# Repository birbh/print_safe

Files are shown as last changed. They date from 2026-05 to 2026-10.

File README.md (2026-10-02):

# print_safe
Print safe is a smart biometric storage system designed for students and teachers to securely store their personal belongings.
This project combines fingerprint based access controls,breach detection and activity logging which helps in preventing the unauthorized access.

Screenshot 2026-10-03 at 1 48 07 AM

## What is this project??
Print safe is an intelligent locker system that allows only authorized person to access stored items using their fingerprint.

Unlike basic locks; it doesnt just opens or closes it but::
- Verifies the identity using fingerprint sensor
- Detects forced access or tampering
- Logs all the access attempts(all including successful and failed one) 

This thing makes it suitable for places like schools,hostels and even a shared living spaces.

## How do you use it? 

1. For Daily Use:
    - Place your registered finger on the sensor:

    1. If fingerprint matches:
        - Servo rotates to unlock the storage
        - Green LED will turn on indicating success
        - A success beep will sound from the buzzer
        - Oled display will show "Access Granted" along with clock
        - The safe will automatically lock after 5 secs(initially)
    2. If fingerprint does not match:
        - Red LED will turn on indicating failure
        - A failure beep will sound from the buzzer
        - Oled display will show "Access Denied" 
    - To lock manually:
        - Press the green push button switch to lock the safe immediately
        - Oled display will show "Door Locked"

2. For Admin Use:
    - To enter admin mode:
        - Press and hold both the green and red push button switch for 5 seconds 
        - The safe will play double beep and oled will show "Admin Mode" and then "Place finger to register"
        1. To register a new fingerprint:
            - Place the new finger on the sensor
            - The system will capture first scan and prompt 'Remove finger'
            - Lift the finger from the sensor
        2. When screen prompts 'Place same finger again':
            - Place the same finger again on the sensor to confirm
        - If successfull, buzzer will play a success tone and oled will show "Fingerprint Registered"

3. Security and resets:
    - Tamper alarm:
        - If an unregistered finger is scanned 3 times in a row, the system will trigger a tamper alarm:
            - Buzzer will sound continuously with loud beeps
            - Red LED will flash rapidly
            - The biometric system will be locked to prevent further attempts
    - To reset the system:
        - Press the red push button which is hidden in the side of the safe
        - This will reset the siren
        - Clear the failed attempt count
        - Allow users to try accessing again
        - Again ready to scan fingerprints

## Story behind this:

### Why am i making this? 
I lived in my school's hostel in my school life. The main problem of hostel life was that my belongings never stayed in my place. Someone always came to my place and misplace my personal belongings, which would frustate me and I used to be very angry as:
- my items were not always where i left them
- there was no way to know who accessed them
- privacy was very hard to maintain

To solve this problem for hostel students, I thought of creating a system to:
- protect belongings
- ensure authorized access
- let user know if system was tampered or not

### How the idea came in my mind?
The idea actually came from my own room at home. One day while i was sitting in my bed, I thought that I don't have privacy maintained in my room. While i was sleeping i thought of keeping a fingerprint scanning device in my room's entrance that would only unlock the room if the fingerprint would match to me. I thought,'Why not make my own custom device at home buying all the parts from the market🤔'. But I never made it 😭.

**print_safe** is my attempt to bring these ideas to life, solving real world problem I personally faced.

## Project preparation instructions:

Printsafe is designed to be fully robust, utilizing mechanical fastners and 3d-printed components.

### Component fastening instructions:
1. Dev boards(Arduino,rtc,boost conv.,charging module,etc): 

    They are mounted to the floor of enclosure using screws through its screw mounting holes.
2. Locking Servos:

    They are slid into custon 3D-printed mounting cages(as in the 3D model) and secure tightly with screws to prevent torsion during locking sequences.
3. Enclosure Door:

    Attached to the main body via dual screw mechanical hinge layout.
4. Door alignment and security:

    A high strength magnetic latch is alighed on the interior frame to provide tactile door retention, ensuring the door remains fixed to the frame so the servo deadbolts can smoothly engage and lock the system.

### Step by step assembly:
1. Prepare the shell:

    3D print the main enclosure body and door panel using the provided 'CAD' files in the repo(recommended: PLA/PETG).
2. Mount the core electronics:

    Secure the Arduino and other similar electronic componects directly into the 3Dprinted mounts given in CAD files as in Onshape.
    Similarly using the dedicated heaavy duty double sided tape of breadboards mount it into the wall as in CAD.Many breadboards already come with a peel-and-stick adhesive backing. Clean both the back of the breadboard and the wall thoroughly before applying.
3. Install servo mounts:

    Screw the 3D printed servo brackets into the interior left wall as in CAD. Slide the servos into the brackets and secure them easily.
4. Hinge and latch attachment:

    Screw the physical hinge to both the interior side wall and the door panel.Mount the magnetic latch components to ensure the tight, aligned seal when the door swings shut.
5. Calibrate the lock position:

    Power the electronics so the servos rotate to their default locked positions, then attach the locking arms to perfectly block door path when closed.
(NOTE: the 3d models are available in fully assembled and parts form in the repo itself. they are refecenced mostly from grabcad and other 3d model libraries.)

### What was challenging and things to be noted??(overall)
There were many challenges making this project. Here i am listing some important things to be noted to make this project on the basis of what i faced in irl build.
- First, it was challenging to make this project fully eco-friendly by using only cardboards and papers. Every small to big things for the project were made from cardboard but for anyone making this I would recommend using a 3d printed case and components which would help a lot in saving time and efficiency.(I couldnt use 3d printed parts cause it takes 3-4 months and huge tax to deliver from abroad and there are not trusted 3d printing platform in my country.
- The logic behind the door opening and closing seems easy in CAD but its a bit complicated as, in my case, servo didnt directly attach to the door so I was forced to use a cardboard extension which attaches to servo head and the door too. But doing this made the cardboard extension move left and right along the door when the servo started to work. So to tackle this I applied the hot glue to the other end of extension and attached it to door and instantly turned and run the device 4 to 5 times which made the glue flexible and the problem was somehow solved but i found that the door dosnt fully close due to the flexible glue. so for this prototype version this issue was not solves and i managed to close it with my hand for the remaining part which then would attach to the magnets inside and holds the door in fixed position. Hence, the 3d printed fixed parts could have solved it.
- Also keep in mind that you dont join the boost converter in opposite direction as it would burn the internal components and you'll have to buy a new one as i did.
- Make sure the batteries are connected in parallel as i. did which would provide a good balanced voltage to the boost converter. 
- This time when i tried to attach the oled, fingerprint sensor and leds to the cardboard door, they were so heavy for the cardboard to handle so i had to change the whole design if my door only letting the oled display attach to the door while moving.
- Last challenge was to provide the essential torque to the door through servos to overcome the magnetic forse between the magnets attached to the end of the door and inner wall of door. So to match the torque of servos I taped the magnet's outer parts and then attached to the door which eventually reduced the magnetic force between the magnets and it was easier for servos to overcome the force. So i recommend using more powerful servos than the standard blue SG90 servos.

That's it!!! If you keep these challenges in mind and work for project, you'd definitely make this project easily in most efficient way.

## why this and why is it unique?
- its not just a lock but decision based security system
- combines verification + intrusion + logging
- designed for real world student problems

## where can it be used ??
- hostel lockers
- school storage system
- personal drawers and cabinets
- shared living spaces

## IRL Build:
### Pictures:
tempImageHhVQ3i
tempImage1bL4IE
tempImageRyGA7T
tempImageo10fXb
tempImage0Veda7
tempImageZshb4o
tempImagegbeKXF
tempImagegSR62w

### Demo Video:
Youtube: [Demo Video](https://www.youtube.com/watch?v=nzNCS3ORe8U)

## CAD:
Screenshot 2026-08-04 at 6 19 32 PM
Screenshot 2026-08-04 at 6 20 45 PM
Screenshot 2026-08-04 at 6 21 53 PM
Screenshot 2026-08-04 at 6 22 24 PM
Screenshot 2026-08-04 at 6 29 24 PM
Screenshot 2026-08-04 at 6 30 27 PM

For those who want to see full design, here's the like to the Onshape CAD model:

[Onshape Model](https://cad.onshape.com/documents/6a9e66424898c3a5d22b5a59/w/668f054415e8574befa880c0/e/08491907242ab19b0f76189a)

## Circuit Diagram:
I made the circuit diagram for my project using tikercad. Due to absence of required components i have used Breadboard to complete the circuit diagram and used the notes feature in tinkercad😅.

   ### SS:
   Main circuit
battery,charging,boost circuit

   ### Links to tinkercad:
   
   [Main circuit](https://www.tinkercad.com/things/bx13RGkoUNs-printsafe-cc/editel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)
   
   [Battery and charging circuit](https://www.tinkercad.com/things/15RenR3HXBn-charging-and-boost/editel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)

## Components required(planned):

- Arduino uno with cable
- AS608 Fingerprint Module
- Servo motor
- Leds
- Active Electronic Buzzer
- Resistors (10k Ω)
- Resistors (220 Ω)
- WIRES
- Breadboard
- Push Button Switches
- 18650 Battery Holder
- 18650 Lithium-Ion Battery
- TP4056 Charging Module
- MT3608 Boost Converter(or equivalent)
- I2C OLED Display 0.96 inch
- DS3231 RTC Module
- ESP8266 NodeMCU(optional)
- 1000μF (Polarized)(greater than 5V)
- Switch (on/off)
- Battery to DC barrel jack(for arduino)
- 3D models as stated above.

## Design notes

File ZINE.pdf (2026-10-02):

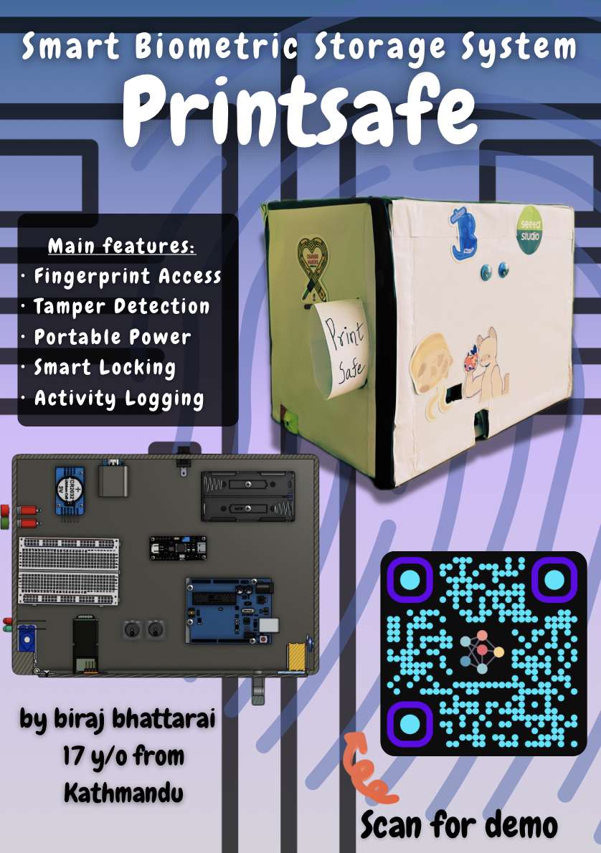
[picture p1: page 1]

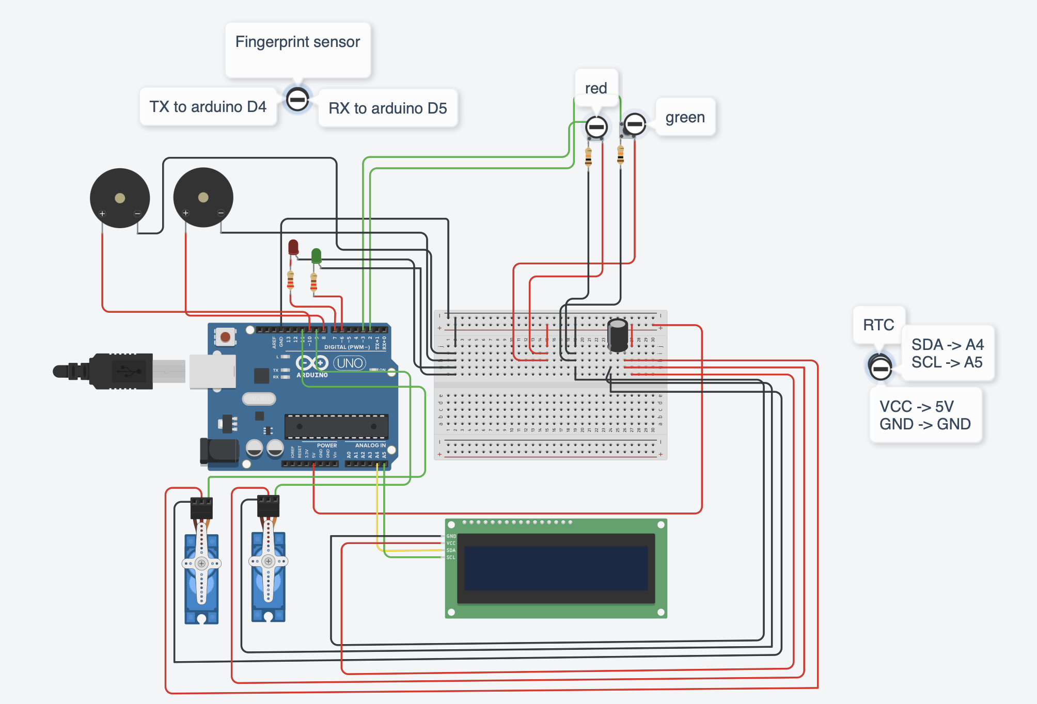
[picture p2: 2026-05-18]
Circuits/Main circuit.png

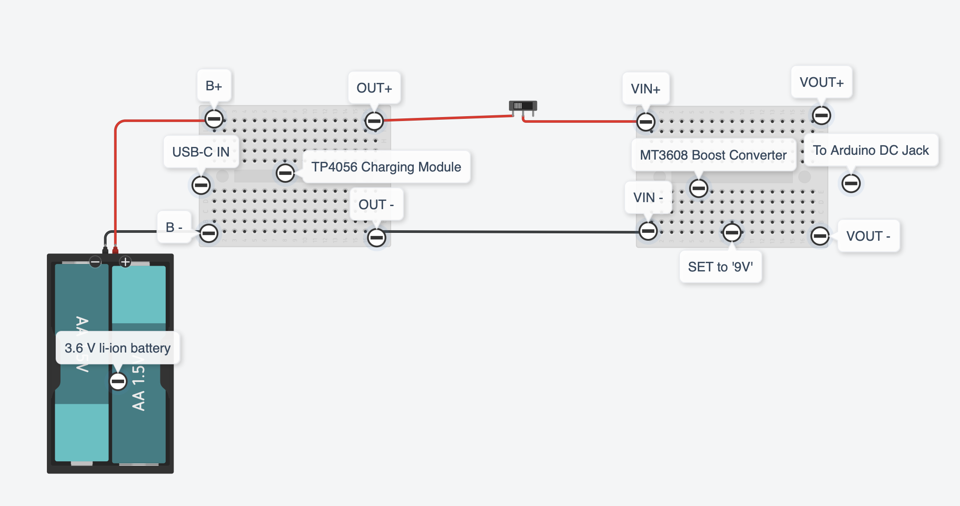
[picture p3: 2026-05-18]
Circuits/battery,charging,boost circuit.png

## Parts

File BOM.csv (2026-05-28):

Items | Price | Link | Quantity
Arduino uno with cable | ~20$ | https://shorturl.at/WWEXE | 1
AS608 Fingerprint Module | $15-20$ | https://shorturl.at/U69mB | 1
Servo motor | $8 | https://shorturl.at/Ip8lg | 2
Leds | $7 | https://shorturl.at/RFGpo | Pack
Active Electronic Buzzer | ~$7 | https://shorturl.at/qj3BP | Pack
Resistors (10k Ω) | $6 | https://acesse.one/ls03mpb | Pack
Resistors (220 Ω) | $5 | https://l1nk.dev/5dzzufx | Pack
Wires(jumper) | $8 | https://l1nk.dev/i9meakx | Pack
Wires(Normal) | ~4$ | https://shorturl.at/ygMDc | Pack
Aluminium foil(optional) | $9 | https://acesse.one/0dw1c65 | 1
Breadboard | $10 | https://l1nk.dev/uzbsl38 | 1
Push Button Switch | $3 | https://l1nk.dev/vnitg2r | 2
18650 Battery Holder | $3 | https://l1nk.dev/oosg72w | 1
18650 Lithium-Ion Battery | $3 | https://l1nq.com/20qpqqt | 1
TP4056 Charging Module | $6 | https://l1nk.dev/wedzzh9 | 1
MT3608 Boost Converter | $6 | https://l1nk.dev/9jh41ry | 1
I2C OLED Display 0.96 inch | $8 | https://l1nk.dev/515rwpb | 1
DS3231 RTC Module | $5 | https://l1nk.dev/nx8q5ky | 1
ESP8266 NodeMCU(optional) | $7 | https://l1nk.dev/9cr6knm | 1
M3 Screw Set(optional) | $6 | https://l1nk.dev/izsoxws | Pack
Acrylic Sheet(Optional) | $9 | https://acesse.one/pnp6sq5 | 1
Mini Hinges | $4 | https://l1nk.dev/g1qcra8 | 2
Magnetic Latch | $7 | https://l1nk.dev/61dy1q1 | 1
1000μF (Polarized)(greater than 5V) | $3-$7 | https://www.ebay.com/itm/255390041576 | 1
Switch (on/off) | ~2$ | https://tinyurl.com/ycyaypbw | 1
Battery to DC barrel jack(for arduino) | ~1$ | https://shorturl.at/GKWPJ | 1
3D printing filament | ~$8-$14 | https://l1nk.dev/jvyhtj1 | 1
Total: | ~170$

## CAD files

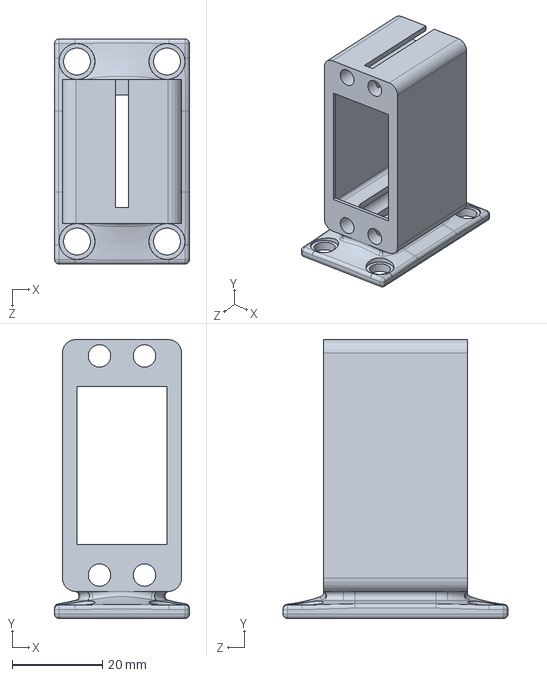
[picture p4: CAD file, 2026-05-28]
CAD/Parts files/Servo Mount (Standing).SLDPRT
30.0 x 62.0 x 50.0 mm

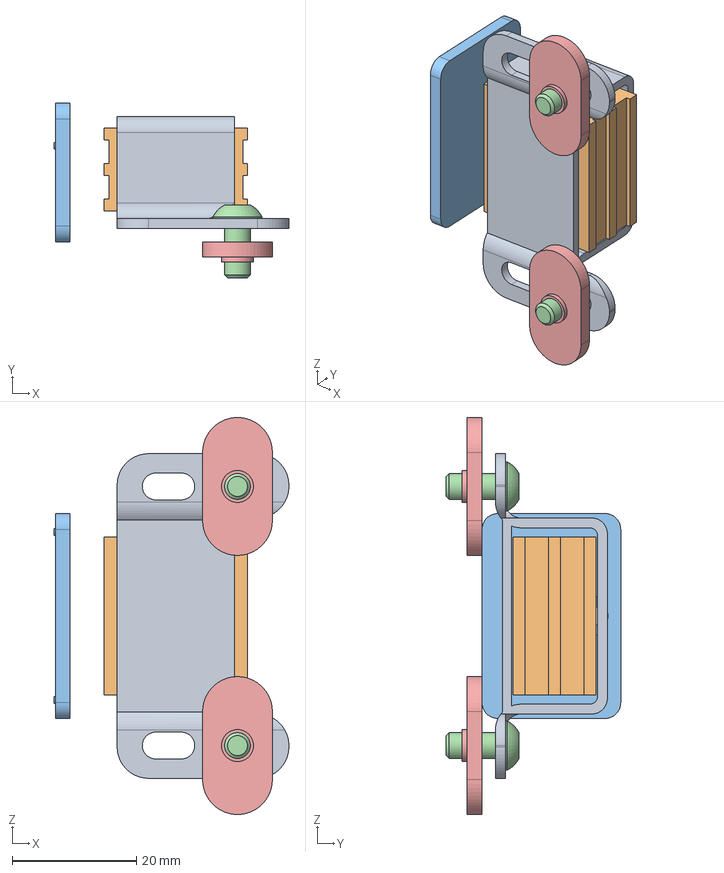
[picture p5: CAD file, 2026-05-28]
CAD/Parts files/2090.stp
37.8 x 28.1 x 64.0 mm
2090_a
2090_magnet
2090_b

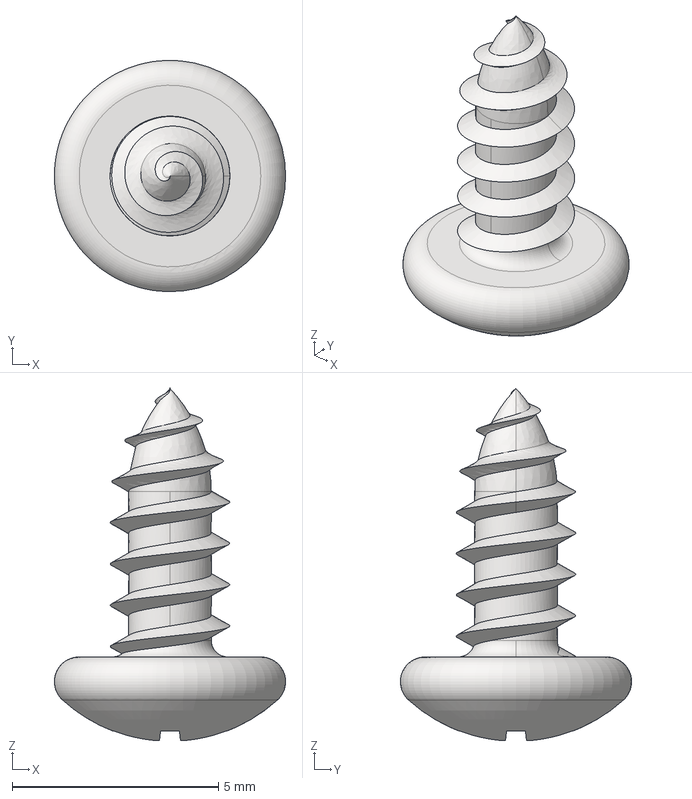
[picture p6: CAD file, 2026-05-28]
CAD/Parts files/lmed scc.stp
5.60 x 5.60 x 8.52 mm

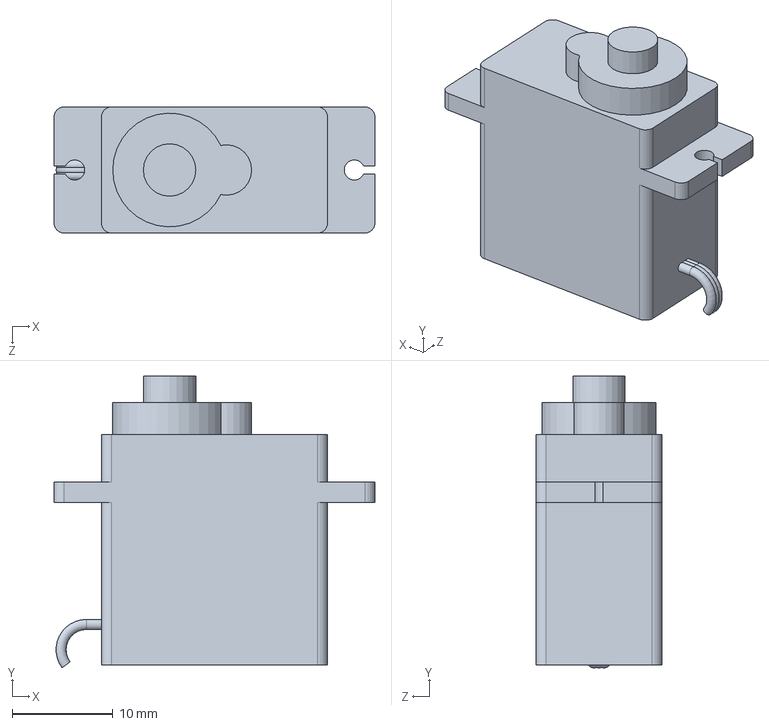
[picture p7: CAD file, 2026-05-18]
CAD/Parts files/Servo_SG90.SLDPRT
31.8 x 28.9 x 12.5 mm

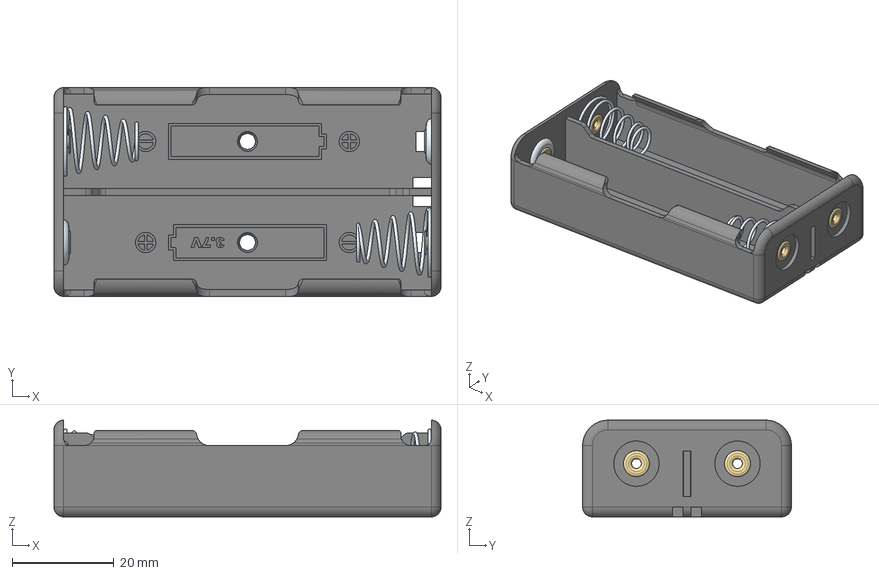
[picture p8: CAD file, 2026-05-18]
CAD/Parts files/BATTERY HOLDER x2.stp
76.0 x 41.0 x 19.0 mm
Porta baterias 2x18650
Contacto_Helice_v2.0 x 2
Contacto_plano_v1.0 x 2
remache_v1.0 x 4

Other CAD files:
CAD/Assemblies/Main assembly.step
CAD/Assemblies/box.step
CAD/Parts files/MoboSpeakerHolder.step
CAD/Parts files/Part Studio 1.step
CAD/Parts files/ActiveBuzzer_TMB12A05.step
CAD/Parts files/Fingerprint Reader.step
CAD/Parts files/Green Push Button.step
CAD/Parts files/TP4056_Charging_Module_Type_C.step
CAD/Parts files/LED D5 - Red.step
CAD/Parts files/Red Push Button.step
CAD/Parts files/Part Studio 2.step
CAD/Parts files/LED D5 - Green.step
CAD/Parts files/DS3231 RTC.step
CAD/Parts files/M4 Hex Screw v2.step
CAD/Parts files/Mensan KP-01 Plastik Kulp.SLDPRT
CAD/Parts files/OLED TEMU 0.96 in.stp
CAD/Parts files/Wood_Screw_Flat_Head_Phillips.SLDPRT
CAD/Parts files/bolt.SLDPRT
CAD/Parts files/m3-5mm.sldprt

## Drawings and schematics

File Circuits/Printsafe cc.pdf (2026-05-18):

A

1 | 2 | 3 | 4 | 5 | 6

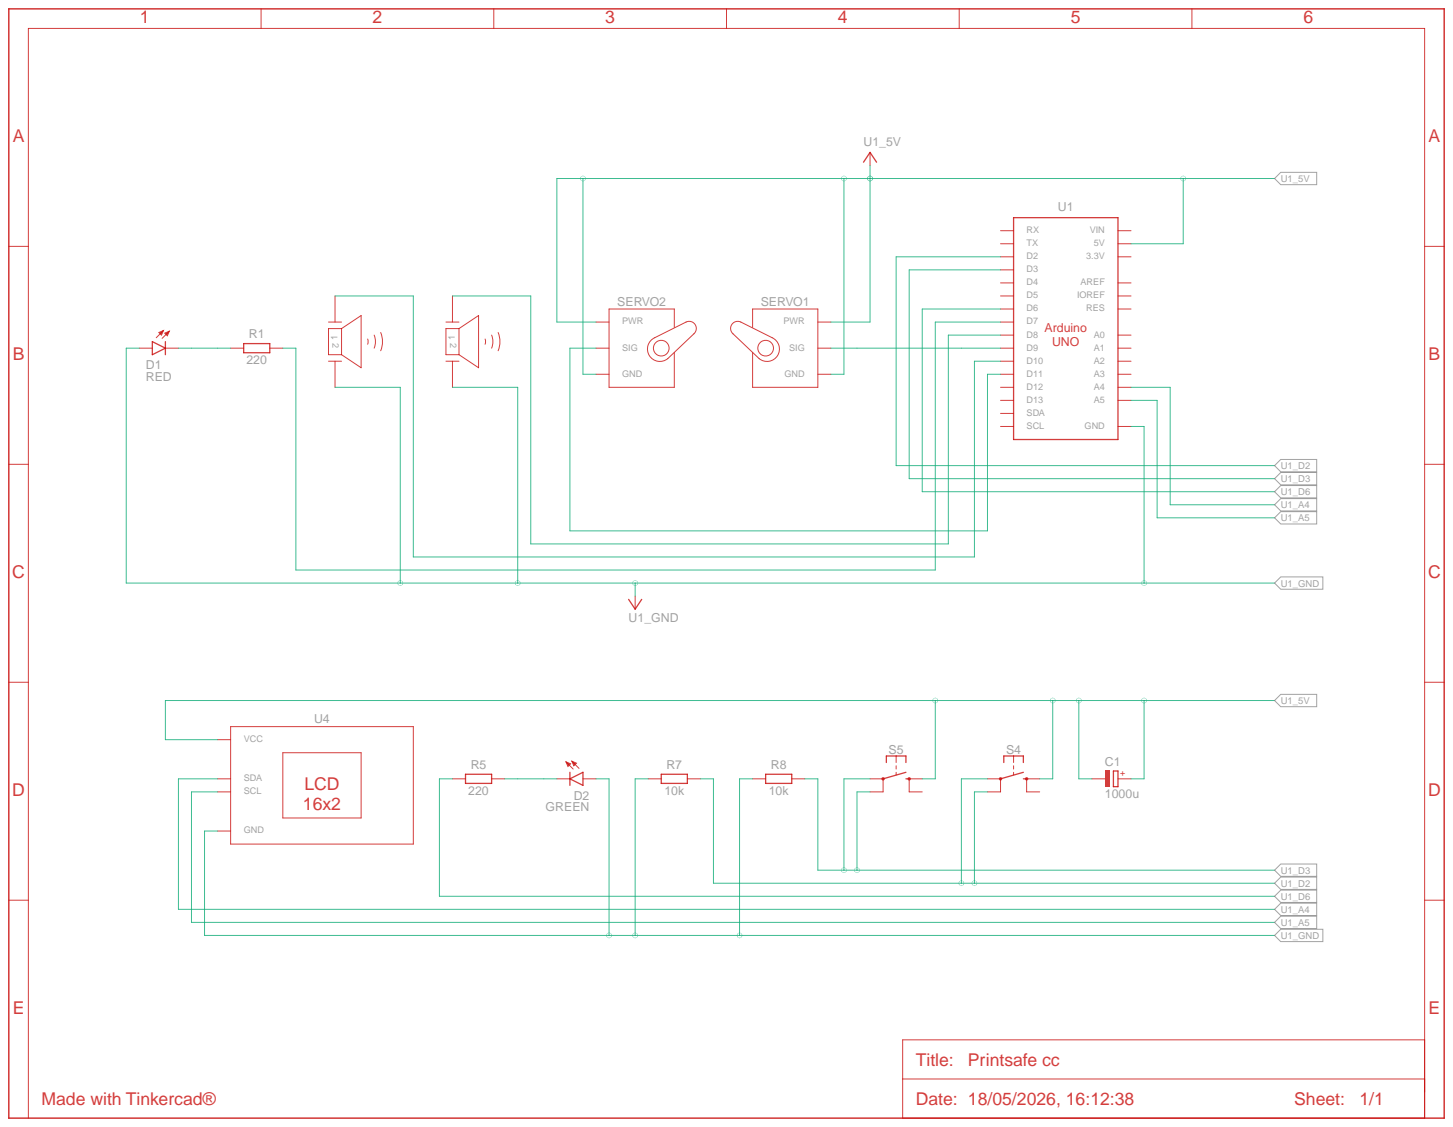
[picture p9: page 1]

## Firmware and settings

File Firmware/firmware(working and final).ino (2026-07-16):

#include <Servo.h>
#include <Adafruit_Fingerprint.h>
#include <Wire.h>
#include <RTClib.h>
#include <Adafruit_GFX.h>
#include <Adafruit_SSD1306.h>

// --- OLED Screen Configuration ---
#define SCREEN_WIDTH 128
#define SCREEN_HEIGHT 64
#define OLED_RESET    -1 
Adafruit_SSD1306 display(SCREEN_WIDTH, SCREEN_HEIGHT, &Wire, OLED_RESET);

// --- Verified Pin Allocations ---
const int greenBtnPin = 4;    // Green Button: Manual Lock / Admin Combo
const int redBtnPin = 5;      // Red Button: Hidden Alarm Reset / Admin Combo
const int greenLedPin = 6;
const int redLedPin = 7;
const int buzzerAPin = 8;     
const int servoupPin = 9;     
const int buzzerBPin = 10;    
const int servodownPin = 11;   

// --- Object Initializations ---
Servo servoup;
Servo servodown;
RTC_DS3231 rtc;

// Fingerprint Sensor Serial Configuration
SoftwareSerial mySerial(2, 3);
Adafruit_Fingerprint finger = Adafruit_Fingerprint(&mySerial);

// --- Global System State Variables ---
int failedAttempts = 0;
const int maxFailedAttempts = 3;
const int stepDelay = 15; 

bool isLocked = true;          // Tracks the physical lock status of the vault
bool systemBlock = false;       // Hardlock flag when tamper alarm is tripped
unsigned long unlockTime = 0;  // Tracks auto-relock window countdowns
const unsigned long autoLockDelay = 30000; // 30 seconds lock window

void setup() {
  Serial.begin(9600);
  delay(500); 
  Serial.println(F("\n============================================="));
  Serial.println(F("         PRINTSAFE PRO STANDALONE FIRMWARE    "));
  Serial.println(F("============================================="));

  // Configure Button Pins with Internal Pull-Ups
  pinMode(greenBtnPin, INPUT_PULLUP);
  pinMode(redBtnPin, INPUT_PULLUP);
  
  pinMode(greenLedPin, OUTPUT);
  pinMode(redLedPin, OUTPUT);
  pinMode(buzzerAPin, OUTPUT);
  pinMode(buzzerBPin, OUTPUT);

  // Initialize OLED
  if(!display.begin(SSD1306_SWITCHCAPVCC, 0x3C)) { 
    errorBlink(3); 
  }
  
  display.clearDisplay();
  display.setTextSize(1);
  display.setTextColor(SSD1306_WHITE);
  display.setCursor(20, 25);
  display.setTextSize(2);
  display.println(F("PRINTSAFE"));
  display.display();
  delay(1500);

  // Initial Servo Alignment (Locked State at 0 Degrees)
  servoup.attach(servoupPin);
  servodown.attach(servodownPin);
  servoup.write(0);
  servodown.write(0); 
  delay(200);
  servoup.detach(); // Cut power to prevent inrush brownouts during setup
  servodown.detach();
  isLocked = true;

  // Initialize Clock
  if (!rtc.begin()) {
    updateOLEDStatus(F("RTC ERROR"), F("Check Wiring"));
    errorBlink(1); 
  }

  // Initialize Fingerprint Sensor
  mySerial.begin(57600);
  finger.begin(57600);
  delay(500); 
  if (!finger.verifyPassword()) {
    updateOLEDStatus(F("AS608 ERROR"), F("Scanner Missing"));
    errorBlink(2); 
  }

  // System Armed Beep
  digitalWrite(greenLedPin, HIGH);
  digitalWrite(buzzerAPin, HIGH); delay(100);
  digitalWrite(buzzerAPin, LOW);
  digitalWrite(greenLedPin, LOW);
}

void loop() {
  // --- BUTTON ROUTINE 1: HIDDEN RED RESET BUTTON ---
  if (digitalRead(redBtnPin) == LOW) {
    if (systemBlock) {
      resetTamperSystem();
    }
  }

  // --- SECURITY CHECK: IF SYSTEM IS BLOCKED, FREEZE UNTIL RED RESET ---
  if (systemBlock) {
    displayRapidTamperFlash();
    return; 
  }

  // --- BUTTON ROUTINE 2: GREEN MANUAL LOCK BUTTON ---
  if (digitalRead(greenBtnPin) == LOW && !isLocked) {
    executeManualRelock();
  }

  // --- BUTTON ROUTINE 3: ADMIN MODE COMBINATION TRIGGER ---
  if (digitalRead(greenBtnPin) == LOW && digitalRead(redBtnPin) == LOW) {
    unsigned long holdStart = millis();
    bool holdSuccess = true;
    
    while (millis() - holdStart < 5000) {
      if (digitalRead(greenBtnPin) == HIGH || digitalRead(redBtnPin) == HIGH) {
        holdSuccess = false;
        break;
      }
      updateOLEDStatus(F("ENTERING ADMIN"), "Hold: " + String((5000 - (millis() - holdStart)) / 1000) + "s");
      delay(100);
    }
    
    if (holdSuccess) {
      runAdminRegistrationMode();
    }
  }

  // --- AUTOMATIC RELOCK ENGINE ---
  if (!isLocked && (millis() - unlockTime >= autoLockDelay)) {
    executeAutomaticRelock();
  }

  // --- REFRESH ARMED STANDBY DISPLAY ---
  refreshStandbyScreen();

  // --- SCAN BIOMETRIC MATRIX ---
  getFingerprintID();
  delay(50); 
}

// --- Biometric Authentication Processing Core ---

int getFingerprintID() {
  while(mySerial.available() > 0) { mySerial.read(); }

  uint8_t p = finger.getImage();
  if (p == FINGERPRINT_NOFINGER) return -1; 
  if (p != FINGERPRINT_OK) return -1; 

  p = finger.image2Tz();
  if (p != FINGERPRINT_OK) return -1; 

  updateOLEDStatus(F("PROCESSING..."), F("Matching Print"));

  p = finger.fingerFastSearch();

  if (p == FINGERPRINT_OK) {
    failedAttempts = 0; 
    executeUnlockRoutine();
    return finger.fingerID;
  } 
  else if (p == FINGERPRINT_NOTFOUND) {
    failedAttempts++;
    executeAccessDenied();
    return -1;
  } else {
    return -1;
  }
}

// --- Daily Operations UI Routines ---

void refreshStandbyScreen() {
  display.clearDisplay();
  display.setTextSize(1);
  display.setCursor(0, 0);
  display.println(isLocked ? F("SYSTEM: LOCKED") : F("SYSTEM: UNLOCKED"));
  display.drawFastHLine(0, 10, 128, SSD1306_WHITE);
  
  DateTime now = rtc.now();
  display.setCursor(0, 20);
  display.print(F("Time: ")); 
  if(now.hour() < 10) display.print('0'); display.print(now.hour()); display.print(F(":"));
  if(now.minute() < 10) display.print('0'); display.print(now.minute()); display.print(F(":"));
  if(now.second() < 10) display.print('0'); display.print(now.second());

  display.setCursor(0, 48);
  display.println(isLocked ? F("[ PLACE FINGER ]") : F("[ GREEN TO LOCK ]"));
  display.display();
}

void executeUnlockRoutine() {
  if (!isLocked) return; 
  
  display.clearDisplay();
  display.drawRect(0, 0, 128, 64, SSD1306_WHITE);
  display.setCursor(20, 15);
  display.print(F("ACCESS GRANTED"));
  
  DateTime now = rtc.now();
  display.setCursor(20, 40);
  if(now.hour() < 10) display.print('0'); display.print(now.hour()); display.print(F(":"));
  if(now.minute() < 10) display.print('0'); display.print(now.minute()); display.print(F(":"));
  display.display();

  digitalWrite(greenLedPin, HIGH);
  digitalWrite(buzzerAPin, HIGH); delay(250); 
  digitalWrite(buzzerAPin, LOW);

  // Drive Servos to Unlock (Smooth sweep from 0 to 50 degrees)
  moveServos(0, 50);
  
  digitalWrite(greenLedPin, LOW);
  isLocked = false;
  unlockTime = millis(); 
}

void executeAccessDenied() {
  updateOLEDStatus(F("ACCESS DENIED"), "Attempts: " + String(failedAttempts) + "/3");
  digitalWrite(redLedPin, HIGH);
  digitalWrite(buzzerAPin, HIGH); delay(1000); 
  digitalWrite(buzzerAPin, LOW);
  digitalWrite(redLedPin, LOW);

  if (failedAttempts >= maxFailedAttempts) {
    systemBlock = true; 
  }
}

void executeManualRelock() {
  updateOLEDStatus(F("DOOR LOCKED"), F("Manual Lock Pin"));
  digitalWrite(redLedPin, HIGH); delay(200); digitalWrite(redLedPin, LOW);
  
  // Reverse sweep from 50 degrees back down to 0
  moveServos(50, 0);
  isLocked = true;
}

void executeAutomaticRelock() {
  updateOLEDStatus(F("RELOCKING..."), F("Auto Time Timeout"));
  
  // Reverse sweep from 50 degrees back down to 0
  moveServos(50, 0);
  isLocked = true;
}

// --- Power-Optimized Unified Servo Drive Block ---

void moveServos(int startPos, int endPos) {
  // Power up the motor lines right before rotation begins
  servoup.attach(servoupPin);
  servodown.attach(servodownPin);
  delay(30); 

  if (startPos < endPos) {
    for (int pos = startPos; pos <= endPos; pos++) {
      servoup.write(pos);   
      servodown.write(pos); 
      delay(stepDelay);     
    }
  } else {
    for (int pos = startPos; pos >= endPos; pos--) {
      servoup.write(pos);   
      servodown.write(pos); 
      delay(stepDelay);     
    }
  }
  
  delay(150); // Allow physical momentum to finish settling at endpoints
  
  // Cut holding current completely to prevent internal brownout resets
  servoup.detach();
  servodown.detach();
}

// --- For Admin Use: Registration Mode Engine ---

void runAdminRegistrationMode() {
  digitalWrite(buzzerAPin, HIGH); delay(80); digitalWrite(buzzerAPin, LOW); delay(80);
  digitalWrite(buzzerAPin, HIGH); delay(80); digitalWrite(buzzerAPin, LOW);
  
  updateOLEDStatus(F("ADMIN MODE"), F("Booting Profiles"));
  delay(1500);
  
  int id = 1;
  while (id < 128) {
    if (finger.loadModel(id) != FINGERPRINT_OK) {
      break; 
    }
    id++;
  }

  // --- PASS 1: SCAN FIRST PRINT ---
  while (true) {
    updateOLEDStatus(F("ADMIN ACTIVE"), F("Place new finger"));
    int p = finger.getImage();
    if (p == FINGERPRINT_OK) break;
  }

  if (finger.image2Tz(1) != FINGERPRINT_OK) {
    updateOLEDStatus(F("REG FAILED"), F("Image Bad. Aborting"));
    delay(2000); return;
  }
  
  updateOLEDStatus(F("REMOVE FINGER"), F("Lift off glass"));
  digitalWrite(buzzerAPin, HIGH); delay(100); digitalWrite(buzzerAPin, LOW);
  
  while (finger.getImage() != FINGERPRINT_NOFINGER) { delay(100); }

  // --- PASS 2: CONFIRM SAME PRINT ---
  while (true) {
    updateOLEDStatus(F("CONFIRMATION"), F("Place same again"));
    int p = finger.getImage();
    if (p == FINGERPRINT_OK) break;
  }

  if (finger.image2Tz(2) != FINGERPRINT_OK) {
    updateOLEDStatus(F("REG FAILED"), F("Matrix Mismatch"));
    delay(2000); return;
  }

  if (finger.createModel() != FINGERPRINT_OK) {
    updateOLEDStatus(F("REG FAILED"), F("Model Error"));
    delay(2000); return;
  }

  if (finger.storeModel(id) == FINGERPRINT_OK) {
    updateOLEDStatus(F("SUCCESS!"), F("Finger Registered"));
    digitalWrite(greenLedPin, HIGH);
    digitalWrite(buzzerAPin, HIGH); delay(100); digitalWrite(buzzerAPin, LOW); delay(50);
    digitalWrite(buzzerAPin, HIGH); delay(300); digitalWrite(buzzerAPin, LOW);
    digitalWrite(greenLedPin, LOW);
  } else {
    updateOLEDStatus(F("REG FAILED"), F("Storage Write Err"));
  }
  delay(2000);
}

// --- Security, Alerts, and Hard Resets ---

void displayRapidTamperFlash() {
  updateOLEDStatus(F("🚨 LOCKOUT 🚨"), F("SYSTEM COMPROMISED"));
  
  digitalWrite(redLedPin, HIGH);
  digitalWrite(buzzerAPin, HIGH);
  delay(60);
  digitalWrite(buzzerAPin, LOW);
  
  digitalWrite(redLedPin, LOW);
  digitalWrite(buzzerBPin, HIGH);
  delay(60);
  digitalWrite(buzzerBPin, LOW);
}

void resetTamperSystem() {
  digitalWrite(buzzerAPin, LOW);
  digitalWrite(buzzerBPin, LOW);
  digitalWrite(redLedPin, LOW);
  
  failedAttempts = 0;   
  systemBlock = false;  
  
  updateOLEDStatus(F("ALARM CLEARED"), F("System Ready"));
  digitalWrite(greenLedPin, HIGH);
  digitalWrite(buzzerAPin, HIGH); delay(400); digitalWrite(buzzerAPin, LOW);
  digitalWrite(greenLedPin, LOW);
  delay(1000);
}

void updateOLEDStatus(String header, String subtext) {
  display.clearDisplay();
  display.drawRect(0, 0, 128, 64, SSD1306_WHITE); 
  display.setTextSize(1);
  display.setCursor(10, 15);
  display.println(header);
  display.setCursor(10, 40);
  display.println(subtext);
  display.display();
}

void errorBlink(int blinks) {
  while(1) {
    for(int i=0; i<blinks; i++) {
      digitalWrite(redLedPin, HIGH);
      digitalWrite(buzzerAPin, HIGH); delay(100);
      digitalWrite(buzzerAPin, LOW);
      digitalWrite(redLedPin, LOW);  delay(150);
    }
    delay(1000); 
  }
}

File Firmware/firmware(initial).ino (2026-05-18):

// printsafe initial firmware

#include <Wire.h>
#include <Adafruit_GFX.h>
#include <Adafruit_SSD1306.h>
#include <Adafruit_Fingerprint.h>
#include <RTClib.h>
#include <Servo.h>
#include <SoftwareSerial.h>

//oled set.
#define width 128
#define height 64

Adafruit_SSD1306 display(
    width,height,&Wire,-1
);

//rtc set.
RTC_DS3231 rtc;

//SERVO set.

Servo servoup;
Servo servodown;


//PINS.  
//leds pins.
const int ledgreen = 6;
const int ledred = 7;

//buzzers pins.
const int buzznormal = 8;
const int buzzalarm = 10;

//servos pins.
const int servoupPin = 9;
const int servodownPin = 11;

//pushbutton pins.
const int greenbtn = 2;
const int redbtn = 3;

//fingerprint set.
const int fingerTX = 4;
const int fingerRX = 5;
SoftwareSerial fingerSerial(fingerTX, fingerRX);
Adafruit_Fingerprint finger = Adafruit_Fingerprint(&fingerSerial);


//vars to be used for security
bool alarmactive=false;
bool fingerrec=false;
unsigned long dualpress=0;
bool dualpressactive=false;
int failedattempts=0;
int fingerID=1; 



//SETUP
void setup(){
    Serial.begin(9600);

    // pins
    pinMode(ledgreen, OUTPUT);
    pinMode(ledred, OUTPUT);

    pinMode(greenbtn, INPUT_PULLUP);
    pinMode(redbtn, INPUT_PULLUP);

    pinMode(buzznormal, OUTPUT);
    pinMode(buzzalarm, OUTPUT);

    // servos
    servoup.attach(servoupPin);
    servodown.attach(servodownPin);
    lockdoor();


    //oled
    if(!display.begin(SSD1306_SWITCHCAPVCC, 0x3C)) 
        {
             Serial.println(F("oled failed"));
             while(1);
        }
    //rtc
    if (!rtc.begin()) {
        Serial.println("Couldn't find RTC");
        while (1);
    }

    // fingerprint
    finger.begin(57600);
    if(finger.verifyPassword()){
        Serial.println("Found fingerprint sensor!");
    } else {
        Serial.println("Did not find fingerprint sensor :(");
        while (1)
        {delay(1);}
        
    }
    //start..
    initialmsg();
    readysnd();


}

void loop(){
    seethebuttonsfirst();
    //serial
    if (Serial.available()){
        char input=Serial.read();

        //authorized
        if(input=='1'){
            accessgranted();
        }
        // unauthorized
        else if(input=='0'){
            accessdenied();
        }

    } 
}

//button handler
void seethebuttonsfirst(){
      bool greenpressed= digitalRead(greenbtn)==LOW;
      bool redpressed= digitalRead(redbtn)==LOW;

      if(greenpressed && redpressed){
        if(!dualpressactive){
            dualpressactive=true;
            dualpress=millis();
      }
      //if pressed both for 5 secs fingerprint enroll active.
      if(dualpressactive && (millis()-dualpress>=5000)){
        dualpressactive=false;
        fingerenroll();
    }}
    else if(!greenpressed && !redpressed){
        dualpressactive=false;
    }

    // if only red pressed reset the alarm
    if(redpressed && alarmactive && !greenpressed){
        resetalarm();
    }
    // if only green pressed lock manually. 
    if(greenpressed && !redpressed && !dualpressactive){
        lockdoor();
        showmsg("DOOR LOCKED","MANUAL LOCK");
        delay(500);
    }
}






void accessgranted(){
    failedattempts=0;
    unlockdoor();

    digitalWrite(ledgreen, HIGH);
    digitalWrite(ledred, LOW);
    
    //beep success buzzer
    successbeep();

    //rtc set time
    DateTime now = rtc.now();

//oled display
    display.clearDisplay();
    display.setTextSize(1);
    display.setTextColor(WHITE);

    display.setCursor(0,0);//changable
    display.println("ACCESS GRANTED");

    //show time and date
    display.setCursor(0,20);
    display.print(now.hour());
    display.print(":");
    display.print(now.minute());
    display.print(":");
    display.println(now.second());
    display.display();
    
    Serial.println("Access Granted for authorized person");

    delay(5000);
    digitalWrite(ledgreen, LOW);



}

void accessdenied(){
    failedattempts++;
    digitalWrite(ledred,HIGH);

    //BEEP WARNING BUZZER
    warningbeep();
    showmsg("ACCESS DENIED","UNAUTHORIZED");
    delay (1000);
    digitalWrite(ledred, LOW);

    //if failed attempts more than 3 activate emergency alarm
    if(failedattempts>=3){
        activatealarm();
    }
}

void fingerenroll(){
    fingerrec=true;
    
    // confirmation 2 beep
    digitalWrite(buzznormal, HIGH);
    delay(300);
    digitalWrite(buzznormal, LOW);
    delay(300);
    digitalWrite(buzznormal, HIGH);
    delay(300);
    digitalWrite(buzznormal, LOW);

    showmsg("ADMIN MODE","PLS PLACE FINGER");
    Serial.println("Place your finger on the sensor to enroll.");

    uint8_t enrollresult = getFingerprintEnroll(fingerID);
    //enroll 
    if (enrollresult == FINGERPRINT_OK) {
        showmsg("ENROLLED OK!", "SLOT ID: " + String(fingerID));
        fingerID++; 
        successbeep();
    } else {
        showmsg("ENROLL FAILED", "TRY AGAIN");
        warningbeep();
    }
    delay(4000);
}
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

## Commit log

2026-04-08 add initial bill of materials (BOM)
    [BOM.csv]
2026-05-14 Updated BOM
    [BOM.csv]
2026-05-15 Bom update
    [BOM.csv]
2026-05-16 update BOM and firmware
    [BOM.csv]
2026-05-18 Add CAD images
    Added CAD images
2026-05-18 Enhance README with design links and component list
    Updated the README to include links to Onshape CAD model and Tinkercad circuits, and revised the list of required components.
2026-05-18 UPLOAD REQUIRED FILES
    [Assembly 1 - 1-copper (1).stl, Assembly 1 - 1-copper (10).stl, Assembly 1 - 1-copper (100).stl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]
2026-05-18 reupload corrected files
    [Assembly 1 - 1-copper (1).stl, Assembly 1 - 1-copper (10).stl, Assembly 1 - 1-copper (100).stl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]
2026-05-19 Add new components to BOM
    [BOM.csv]
2026-05-28 parts and readme update
    [2090.stp, BOM.csv, M4 Hex Screw v2.step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]
2026-05-28 Update CAD section with additional images
    Added new images to the CAD section of the README.
2026-05-30 part update
    [LED D5 - Green-Clear.step, Part Studio 2.stl, Wood_Screw_Flat_Head_Phillips.SLDPRT]

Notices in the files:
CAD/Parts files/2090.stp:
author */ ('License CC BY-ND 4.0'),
